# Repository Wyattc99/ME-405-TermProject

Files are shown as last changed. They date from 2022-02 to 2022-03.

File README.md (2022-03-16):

# Term Project
## Authors: Wyatt Conner, Jameson Spitz, Jacob Wong

## Introduction
The purpose of this project was to design a 2D plotter that can interpret an HPGL file and 
draw an image on paper. Our system controls the position of a pen by having our Nucleo 
microcontroller drive two motors, moving the pen along 2 axes. Additionally, the system 
must raise and lower the pen to control when the system is drawing.

## Hardware Design
To control the position of a pen, we designed a two degree of freedom system that operates 
in cylindrical coordinates R and Theta. We drive a lead screw actuator system using a motor 
to move the pen along the radial direction. The pen is secured to a 3D printed housing that 
is pushed by the lead screw along the main shaft of the assembly. The housing also holds a 
solenoid that performs the pen-up/pen-down action of the system.

To control movement of the housing in the theta direction, our system revolves about a pin joint 
connected to one end of a shaft, and a second motor drives a wheel on the other end of the shaft. 
See the images below for a CAD model and an image of the final prototype. All parts were either 
bought online, 3D printed, or found in our local Cal Poly machine shops.

### Assembly CAD Drawing
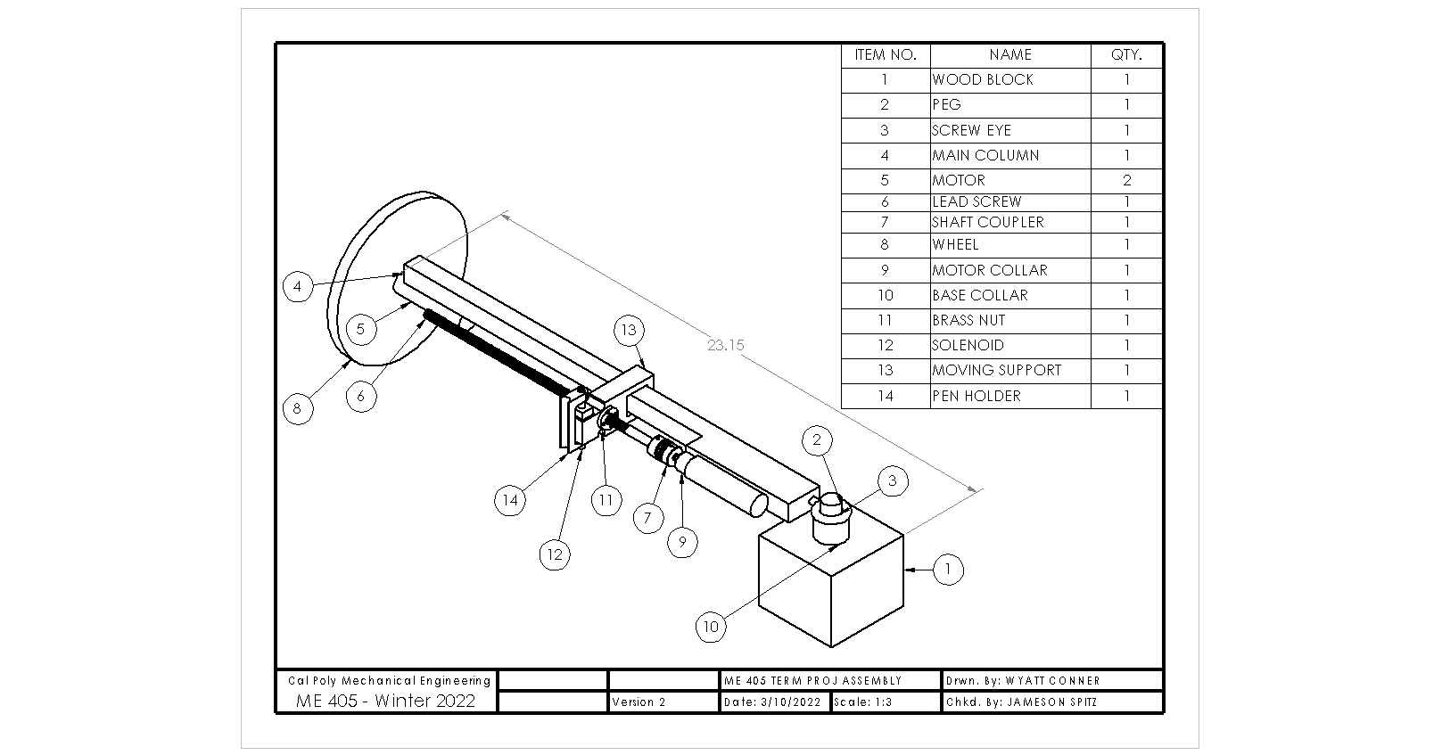
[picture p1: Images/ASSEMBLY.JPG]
Assembly Drawing and BOM


### Physical System Designed
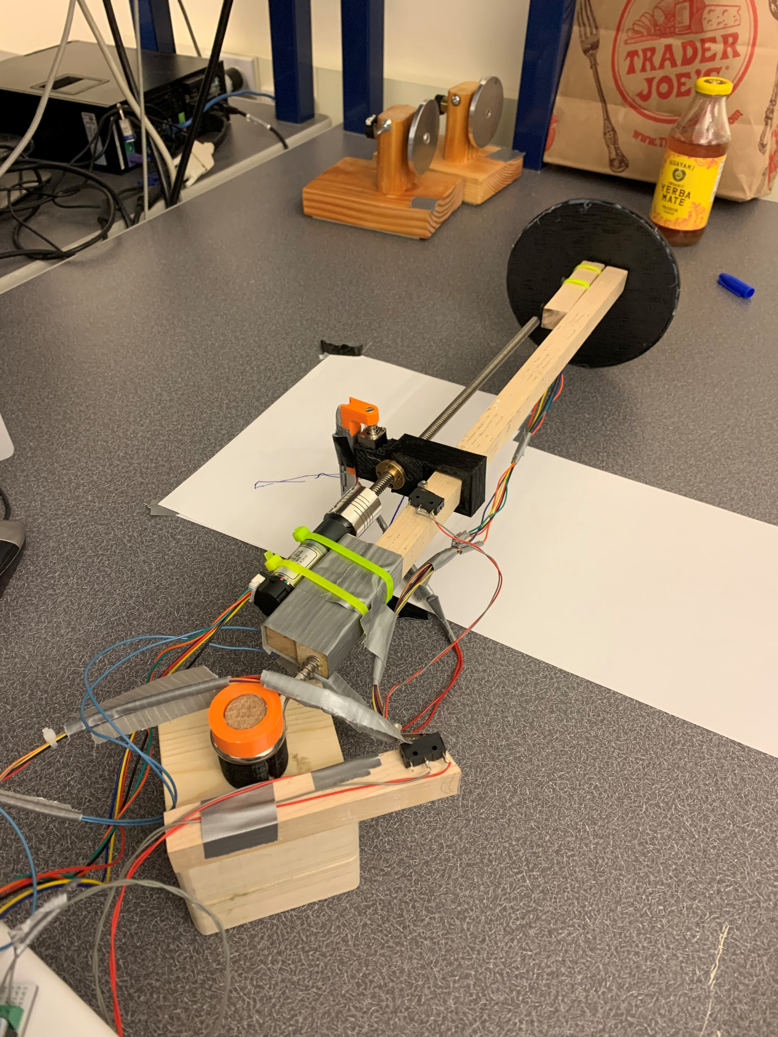
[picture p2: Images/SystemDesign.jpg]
System Design


We needed 12V to power the solenoid. However,  the Nucleo is unable to provide such a voltage. 
Therefore, we use an external 12V-DC power supply, and we constructed circuitry using a MOSFET to 
control this voltage to the solenoid. This allows us to power and unpower the solenoid by setting 
a pin to high or low on the microcontroller. The schematic of the circuitry is shown below.

### Solenoid Wiring Diagram (Transistor and Diode)
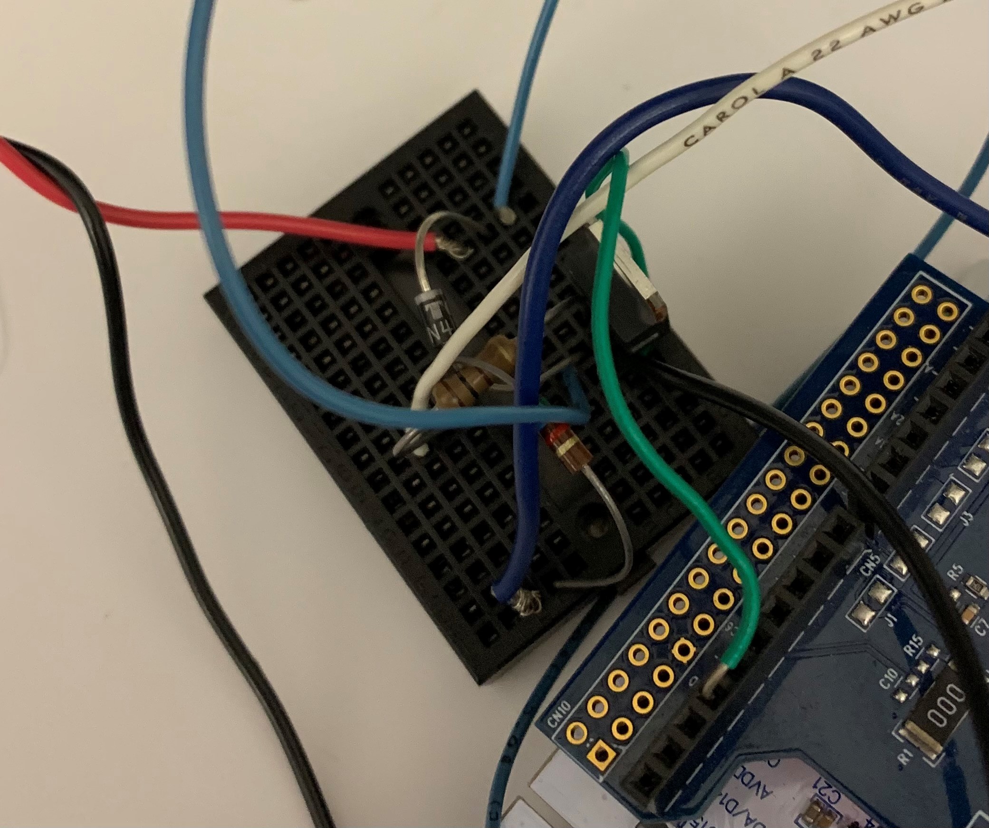
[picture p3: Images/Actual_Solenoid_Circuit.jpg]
Solenoid Wiring1


### Theoretical Wiring Diagram
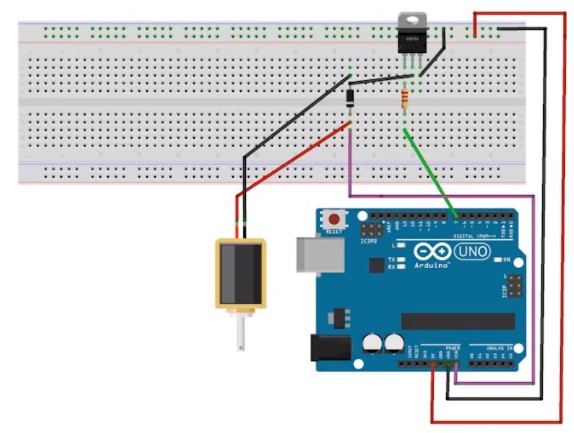
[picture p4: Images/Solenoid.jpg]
Solenoid Wiring2


Lastly, a limit switch is mounted on the main shaft to establish the zero point of the radial 
direction. Whenever the pen housing unit hits the limit switch, it sends a signal to the 
microcontroller to let the software know that housing is at this point.

## Software Design
The software for this project is a cooperative multitasking system that contains five tasks: a 
zeroing task, two tasks to set the desired position of the motors, and two tasks to set the duty
cycle of the motors. The zeroing task named 'Zero Position' sets the encoder position to zero
when the pen housing hits a limit switch, marking the zero position in the radial direction. The
desired position tasks called 'Radial Set Point Control' and 'Theta Set Point Control' reads the
HPGL file and converts X and Y coordinates to R and Theta coordinates. Then, the tasks store 
these coordinates in two queue objects. The two duty cycle tasks, called 'Radial Position Control'
and 'Theta Position Control' gather encoder data and desired position data from the previous two 
tasks. These tasks then implement closed-loop positional control to set the duty cycle going to 
each motor.

To convert X and Y data from the HPGL to R and Theta coordinates in the 'Set Point Control' 
tasks, we needed to derive two kinematic equations, one for R and one for Theta. Hand calculations
for these equations are pictured below.

### Inverse Kinematics Calculations
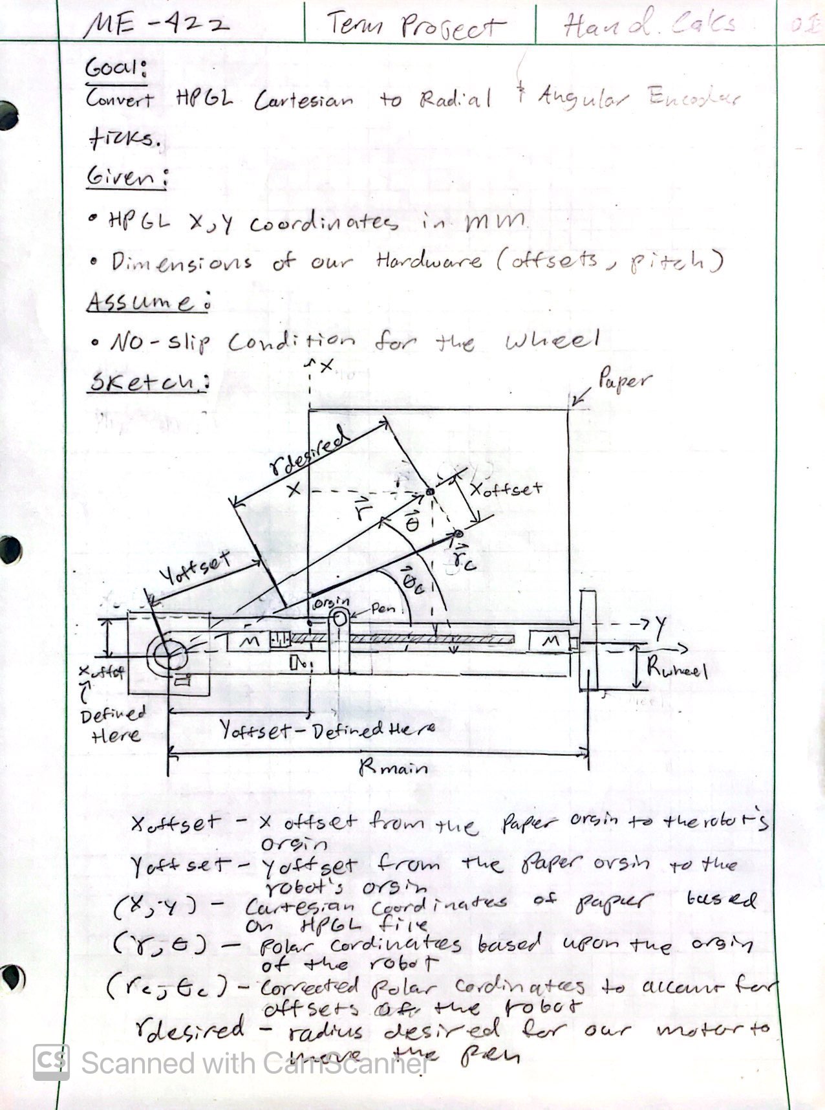
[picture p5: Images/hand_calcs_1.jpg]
Kinematics Sheet 1

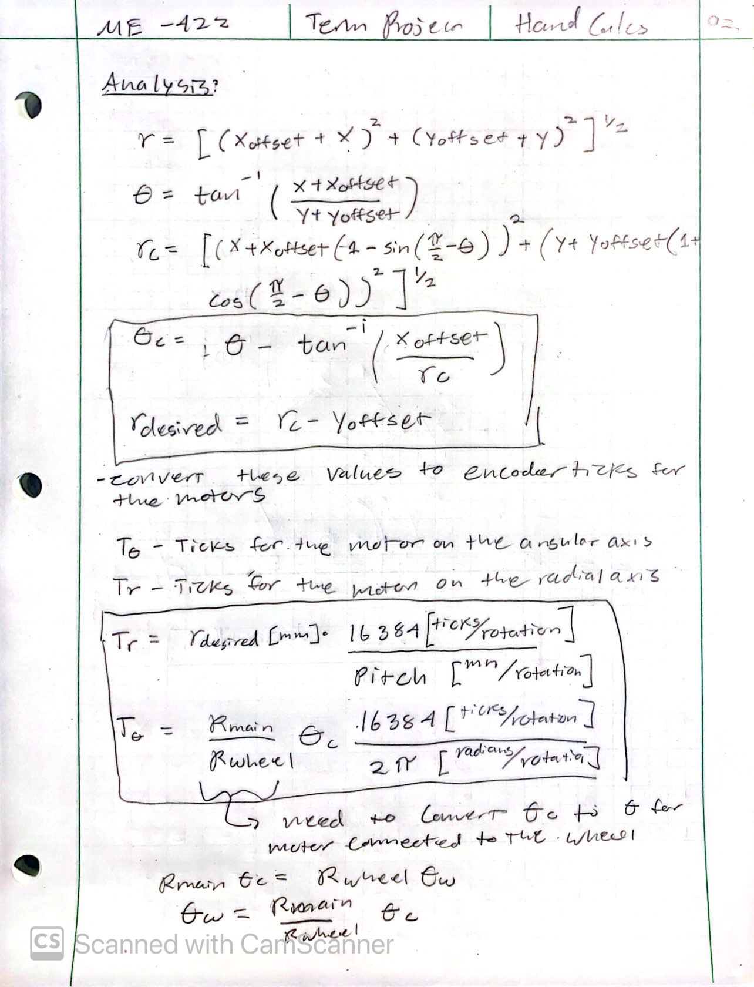
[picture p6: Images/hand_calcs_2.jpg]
Kinematics Sheet 2


Each task is run using a finite state machine (FSM). The most important FSMs are in the 'Radial 
Position Control' and 'Theta Position Control' tasks. Both these task run using a similar FSM 
depicted by the State Transition Diagrm in the image below. In State 0, each task collects a new 
set point, or desired position for the motor. In State 1, each task calculates the error between
actual position (encoder data) and set point. If the error is above a specified threshold, it 
updates the duty cycle of the motor based on the error and returns to State 1. If the error is 
below the threshold, the tasks returns to State 0 to get a new set point. 

See a full description of our software and FSM and Task Diagram in the link to our repository:[Github Pages](https://wyattc99.github.io/ME-405-TermProject/)

## Results
To test our system, we began with testing each individual component separately. We first ran each 
motor to verify that we can control them separately. We next isolated the solenoid to ensure we 
can power and unpower it using the microcontroller. Lastly, we tested the limit switch by itself
and checked if the software can properly detect collision. 

Once we were ready to test the entire system together, our main focus was to verify that our 
kinematic relationships gave accurate results, adjust our threshold value for the error, and to 
tune the controller gains from our positional control loop. This test proved to be challenging,
and unfortunately, our system was unable to achieve satisfactory results. The desired image we
drew in Inkscape was a rectangle, but the image below is the drawing that our system produced.

### Resulting Rectangle
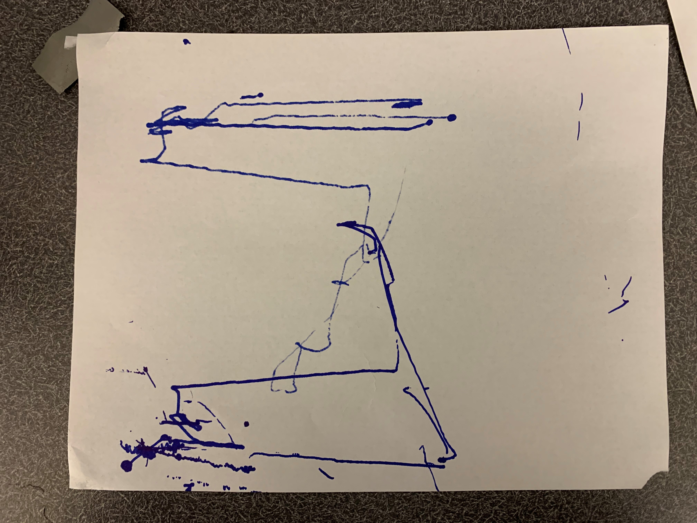
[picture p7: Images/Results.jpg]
Results


## Conclusion and Discussion
Although we were unable to create a successful 2D plotter before the deadline, we found several
issues that could be rectified in the future. One problem that we noticed was that the two
motors would reach their set points out of sync, meaning that one motor would have to wait for 
the other motor. To solve this, we could have interpolated between two setpoints to create 
several 'inbetween setpoints'. This would reduce the inaccuracies caused by the motors meeting
their setpoints at different times.

Another way we could have improved our software was to change the type of controller we used
in our positional control loop. Our current software uses a proportional (P) controller. Instead,
we could have implemented a PI controller to reduce the steady-state positional error. We could 
have even implemented a PID controller to decreased overshoot.

## Bill Of Materials

| Qty. | Part | Source | Est. Cost |
|:----:|:---  |:---|:---:|
|  1 | Wheel | 3D Printing | - |
|  1 | Screw Eye | Home Depot | $4.99 |
|  1 | Lead Screw | Amazon | $12.99  |
|  1 | Solenoid | Digi-Key | $4.95 |
|  3 | Limit Switches | Amazon | $2.00 |
|  1 | Shaft Slider | 3D Printing | - |
|  1 | Pencil/Solenoid Housing | 3D Printing | - |
|  1 | Duct Tape | Home Depot | $6.87 |
|  2 | MOSFET | Friend in 405 | - |
|  1 | Diode | ME 405 Lab | - |
|  3 | Zip Ties | Friend in 405 | - |
|  5 | Wires/Solder | ME 405 Lab | - |
|  2 | Motors | ME 405 Lab | - |
|  1 | Wood Block | Home Depot | $8.25 |
|  1 | Shaft | Home Depot | $6.18 |
|  1 | Shaft Coupler | Amazon | $3.98 |
|  1 | Wooden Peg | Home Depot | $3.48 |

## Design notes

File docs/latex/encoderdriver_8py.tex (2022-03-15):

\hypertarget{encoderdriver_8py}{}\doxysection{src/encoderdriver.py File Reference}
\label{encoderdriver_8py}\index{src/encoderdriver.py@{src/encoderdriver.py}}

This file configures Nucleo pins, timers, and channels for so that it can send voltage to a motor.  

\doxysubsection*{Classes}
\begin{DoxyCompactItemize}
\item 
class \mbox{\hyperlink{classencoderdriver_1_1_encoder_driver}{encoderdriver.\+Encoder\+Driver}}
\begin{DoxyCompactList}\small\item\em Initializes encoder pins, timer, and channel. \end{DoxyCompactList}\end{DoxyCompactItemize}
\doxysubsection*{Variables}
\begin{DoxyCompactItemize}
\item 
\mbox{\Hypertarget{encoderdriver_8py_af3a4bb5350815afb8f1333f182316c40}\label{encoderdriver_8py_af3a4bb5350815afb8f1333f182316c40}} 
{\bfseries encoderdriver.\+my\+\_\+encoder1} = Encoder\+Driver(pyb.\+Pin.\+board.\+PB6, pyb.\+Pin.\+board.\+PB7, 4)
\begin{DoxyCompactList}\small\item\em my\+\_\+encoder1 Encoder object 1. \end{DoxyCompactList}\item 
\mbox{\Hypertarget{encoderdriver_8py_abfefff0f805f0b7f8a9dd10919517436}\label{encoderdriver_8py_abfefff0f805f0b7f8a9dd10919517436}} 
{\bfseries encoderdriver.\+my\+\_\+encoder2} = Encoder\+Driver(pyb.\+Pin.\+board.\+PC6, pyb.\+Pin.\+board.\+PC7, 8)
\begin{DoxyCompactList}\small\item\em my\+\_\+encoder2 Encoder object 2. \end{DoxyCompactList}\end{DoxyCompactItemize}

\doxysubsection{Detailed Description}
This file configures Nucleo pins, timers, and channels for so that it can send voltage to a motor. 

Can send a PWM duty cycle to the motor to control how fast the motor spins. Uses a L6206 motor shield to control motor direction. \begin{DoxyAuthor}{Author}
Jacob Wong 

Wyatt Conner 

Jameson Spitz 
\end{DoxyAuthor}
\begin{DoxyDate}{Date}
26-\/Jan-\/22 
\end{DoxyDate}
\begin{DoxyCopyright}{Copyright}
by Jacob Wong all rights reserved 
\end{DoxyCopyright}

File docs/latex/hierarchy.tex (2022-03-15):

\doxysection{Class Hierarchy}
This inheritance list is sorted roughly, but not completely, alphabetically\+:\begin{DoxyCompactList}
\item \contentsline{section}{task\+\_\+share.\+Base\+Share}{\pageref{classtask__share_1_1_base_share}}{}
\begin{DoxyCompactList}
\item \contentsline{section}{task\+\_\+share.\+Queue}{\pageref{classtask__share_1_1_queue}}{}
\item \contentsline{section}{task\+\_\+share.\+Share}{\pageref{classtask__share_1_1_share}}{}
\end{DoxyCompactList}
\item \contentsline{section}{encoderdriver.\+Encoder\+Driver}{\pageref{classencoderdriver_1_1_encoder_driver}}{}
\item \contentsline{section}{read\+\_\+plotter.\+Hpgl}{\pageref{classread__plotter_1_1_hpgl}}{}
\item \contentsline{section}{limit\+\_\+switch.\+Limit\+\_\+\+Switch}{\pageref{classlimit__switch_1_1_limit___switch}}{}
\item \contentsline{section}{motordriver.\+Motor\+Driver}{\pageref{classmotordriver_1_1_motor_driver}}{}
\item \contentsline{section}{positioncontrol.\+Position\+Control\+Task}{\pageref{classpositioncontrol_1_1_position_control_task}}{}
\item \contentsline{section}{solenoid.\+Solenoid}{\pageref{classsolenoid_1_1_solenoid}}{}
\item \contentsline{section}{cotask.\+Task}{\pageref{classcotask_1_1_task}}{}
\item \contentsline{section}{cotask.\+Task\+List}{\pageref{classcotask_1_1_task_list}}{}
\end{DoxyCompactList}

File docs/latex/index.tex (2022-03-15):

\hypertarget{index_sec_intro1}{}\doxysection{Software Design}\label{index_sec_intro1}
\begin{DoxyVerb}                        Our program will consist of tasks position_control1, position_control2, encoder1, encoder2, and HP-GL. 
                        The position control tasks will control the duty cycle of each motor individually and measure 
                        how many ticks each encoder is from its desired position. As each encoder gets closer to its 
                        desired position, the duty cycles will be decreasing to reach a final position without overshoot 
                        through closed loop position control. The encoder tasks will be responsible for updating, reading, 
                        and setting encoder position for each motor. A critical part to this project is finding a way to 
                        reset the set position for each motor based on the image we want to draw. We imagine that we will 
                        be using a task that gets the desired pencil position through HP-GL, which tells us the set position 
                        in the radial and theta direction for each move of the pencil. Additionally, we will have a solenoid 
                        driver to control whether the solenoid is on or off to move the pencil on and off the paper. Finally, 
                        a limit switch driver will read when the pencil has reached the end of the leadscrew, notifying the 
                        controller the motor needs to stop or switch direction to avoid system failure. 

                        All tasks will be facilitated by a main program that runs each task through a task scheduler. 
                        Additionally, all shared and queued variables will be created within the main file. We expect each 
                        task to share encoder position and duty cycle to control the motor speed. Additionally, there will 
                        be queue values to store encoder position and time data that will be printed at the end of a program run. 

                        With all tasks running simultaneously at different frequencies through the task scheduler, our microcontroller 
                        should be able to successfully control each motor's speed and direction individually to move our pencil in 
                        the radial and theta direction. The most difficult aspect of the code we envision is changing the desired position 
                        of each encoder based on the image we want the system to draw. We will need gain factors to convert a desired 
                        pencil position into radial and axial coordinates and then convert into encoder ticks. These gain values will be 
                        found through testing.
\end{DoxyVerb}
\hypertarget{index_subsec_intro2}{}\doxysection{Task Diagram and Finite State Machines}\label{index_subsec_intro2}
\begin{DoxyVerb}                        Below is the Task Diagram of all tasks used to control the pencil position.
                        \image html TaskDiagram_FinalProj.png

                        Below is the Finite State Machine for our the position control file of one motor.
                        \image html Fsm_TermProj.png
\end{DoxyVerb}
 \begin{DoxyAuthor}{Author}
Jameson Spitz 

Jacob Wong 

Wyatt Conner
\end{DoxyAuthor}
\begin{DoxyCopyright}{Copyright}
CC BY
\end{DoxyCopyright}
\begin{DoxyDate}{Date}
February 24, 2021 
\end{DoxyDate}

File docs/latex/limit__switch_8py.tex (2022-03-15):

\hypertarget{limit__switch_8py}{}\doxysection{src/limit\+\_\+switch.py File Reference}
\label{limit__switch_8py}\index{src/limit\_switch.py@{src/limit\_switch.py}}

This file configures a limit switch to trigger high when our physical system presses the limit switch closed.  

\doxysubsection*{Classes}
\begin{DoxyCompactItemize}
\item 
class \mbox{\hyperlink{classlimit__switch_1_1_limit___switch}{limit\+\_\+switch.\+Limit\+\_\+\+Switch}}
\begin{DoxyCompactList}\small\item\em Initializes the normally open pin on the Nucleo as an input pin. \end{DoxyCompactList}\end{DoxyCompactItemize}
\doxysubsection*{Variables}
\begin{DoxyCompactItemize}
\item 
\mbox{\Hypertarget{limit__switch_8py_a87c9bd543d8a042600c67cf8071ea98a}\label{limit__switch_8py_a87c9bd543d8a042600c67cf8071ea98a}} 
{\bfseries limit\+\_\+switch.\+my\+\_\+lim\+\_\+A} = Limit\+\_\+\+Switch(pyb.\+Pin.\+board.\+PC0)
\item 
\mbox{\Hypertarget{limit__switch_8py_aa92905b475b2bf1bbdf7b00949fcc1cc}\label{limit__switch_8py_aa92905b475b2bf1bbdf7b00949fcc1cc}} 
{\bfseries limit\+\_\+switch.\+my\+\_\+lim\+\_\+B} = Limit\+\_\+\+Switch(pyb.\+Pin.\+board.\+PB0)
\end{DoxyCompactItemize}

\doxysubsection{Detailed Description}
This file configures a limit switch to trigger high when our physical system presses the limit switch closed. 

The file is set up as a class so a user can instantiate mulitple limit switches. We have physically configured the limit switch to be normallly open. \begin{DoxyAuthor}{Author}
Jacob Wong 

Wyatt Conner 

Jameson Spitz 
\end{DoxyAuthor}
\begin{DoxyDate}{Date}
5-\/March-\/22 
\end{DoxyDate}
\begin{DoxyCopyright}{Copyright}
by Jacob Wong all rights reserved 
\end{DoxyCopyright}

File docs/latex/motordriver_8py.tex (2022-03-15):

\hypertarget{motordriver_8py}{}\doxysection{src/motordriver.py File Reference}
\label{motordriver_8py}\index{src/motordriver.py@{src/motordriver.py}}

This file configures Nucleo pins, timers, and channels for so that it can send voltage to a motor.  

\doxysubsection*{Classes}
\begin{DoxyCompactItemize}
\item 
class \mbox{\hyperlink{classmotordriver_1_1_motor_driver}{motordriver.\+Motor\+Driver}}
\begin{DoxyCompactList}\small\item\em Initializes motor pins allowing for the motor to rotate in both directions. \end{DoxyCompactList}\end{DoxyCompactItemize}
\doxysubsection*{Variables}
\begin{DoxyCompactItemize}
\item 
\mbox{\Hypertarget{motordriver_8py_ad9e5193122e62bbfef90dec601759637}\label{motordriver_8py_ad9e5193122e62bbfef90dec601759637}} 
{\bfseries motordriver.\+motor1} = Motor\+Driver(pyb.\+Pin.\+board.\+PB5, pyb.\+Pin.\+board.\+PB4, pyb.\+Pin.\+board.\+PA10, 3)
\begin{DoxyCompactList}\small\item\em motor1 Motor object 1. \end{DoxyCompactList}\item 
\mbox{\Hypertarget{motordriver_8py_a6af998346fc8903e2ad3fde4cac66cfd}\label{motordriver_8py_a6af998346fc8903e2ad3fde4cac66cfd}} 
{\bfseries motordriver.\+motor2} = Motor\+Driver(pyb.\+Pin.\+board.\+PA0, pyb.\+Pin.\+board.\+PA1, pyb.\+Pin.\+board.\+PC1, 5)
\begin{DoxyCompactList}\small\item\em motor2 Motor object 2. \end{DoxyCompactList}\end{DoxyCompactItemize}

\doxysubsection{Detailed Description}
This file configures Nucleo pins, timers, and channels for so that it can send voltage to a motor. 

Can send a PWM duty cycle to the motor to control how fast the motor spins. Uses a L6206 motor shield to control motor direction. \begin{DoxyAuthor}{Author}
Jacob Wong 

Wyatt Conner 

Jameson Spitz 
\end{DoxyAuthor}
\begin{DoxyDate}{Date}
26-\/Jan-\/22 
\end{DoxyDate}
\begin{DoxyCopyright}{Copyright}
by Jameson Spitz all rights reserved 
\end{DoxyCopyright}

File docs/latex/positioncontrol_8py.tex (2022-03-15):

\hypertarget{positioncontrol_8py}{}\doxysection{src/positioncontrol.py File Reference}
\label{positioncontrol_8py}\index{src/positioncontrol.py@{src/positioncontrol.py}}

Control Motor\textquotesingle{}s position based on desired HPGL set points.  

\doxysubsection*{Classes}
\begin{DoxyCompactItemize}
\item 
class \mbox{\hyperlink{classpositioncontrol_1_1_position_control_task}{positioncontrol.\+Position\+Control\+Task}}
\begin{DoxyCompactList}\small\item\em This class contains the methods to create a feed back control system using a motor and encoder. \end{DoxyCompactList}\end{DoxyCompactItemize}

\doxysubsection{Detailed Description}
Control Motor\textquotesingle{}s position based on desired HPGL set points. 

The file can check if the error between a motor position and the setpoint is within reasonable limits and flag for the next setpoint. We use a simple proportional controller to set a proper duty cycle based on the magnitude of the error. \begin{DoxyAuthor}{Author}
Jacob Wong 

Wyatt Conner 

Jameson Spitz 
\end{DoxyAuthor}
\begin{DoxyDate}{Date}
3-\/Mar-\/22 
\end{DoxyDate}
\begin{DoxyCopyright}{Copyright}
by Jameson Spitz all rights reserved 
\end{DoxyCopyright}

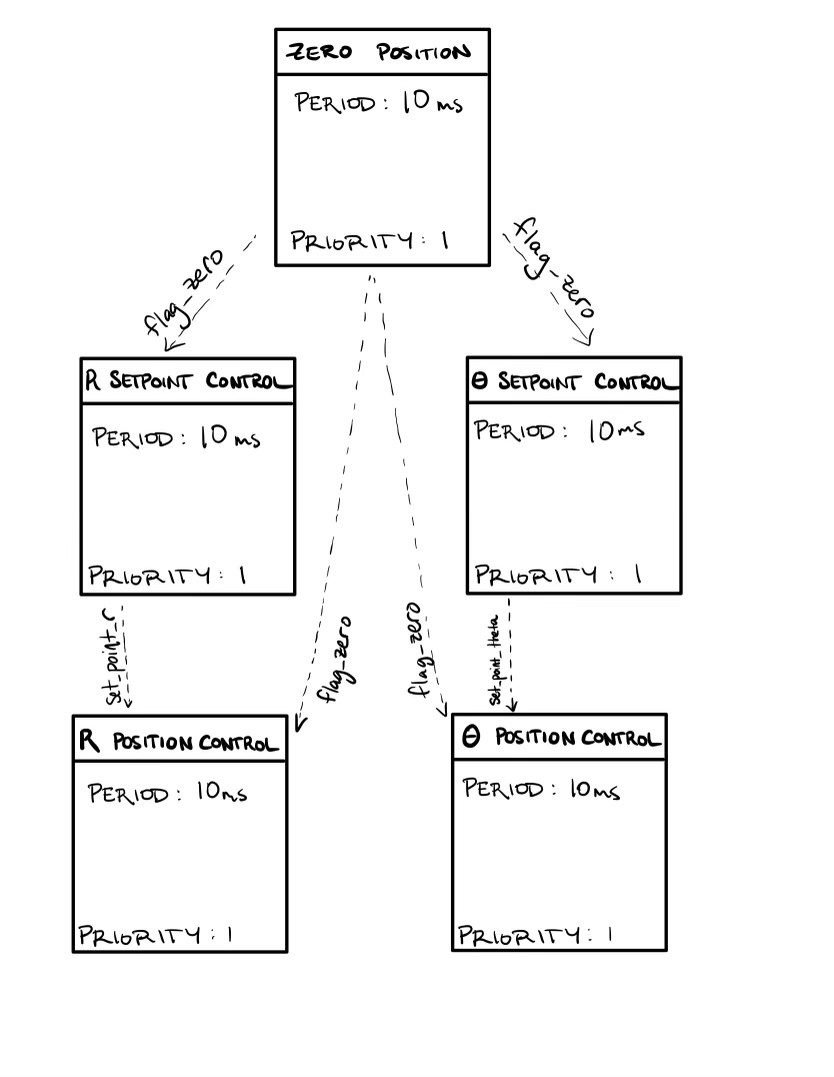
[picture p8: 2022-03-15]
docs/TaskDiagram_FinalProj.jpg

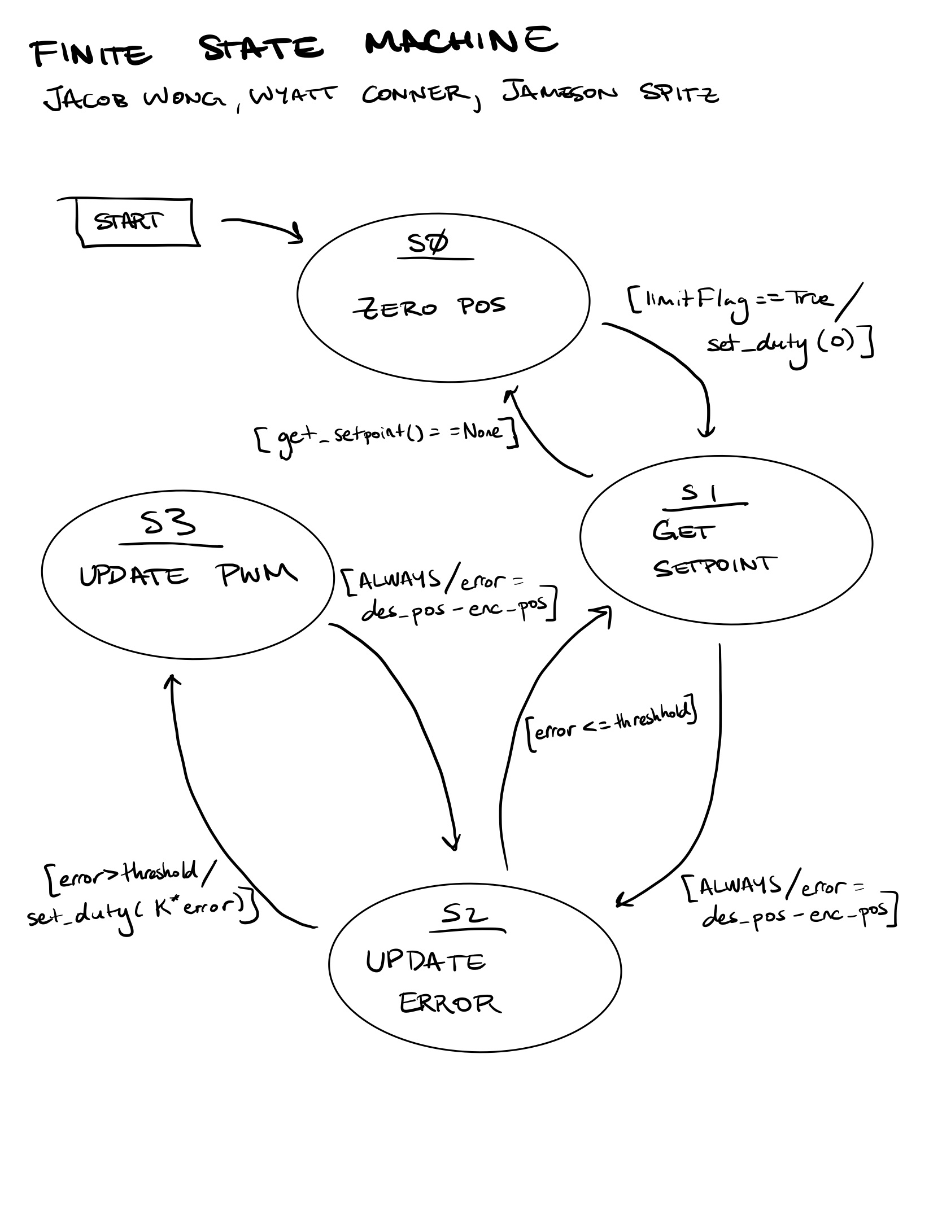
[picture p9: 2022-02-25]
Images/Fsm_TermProj.png

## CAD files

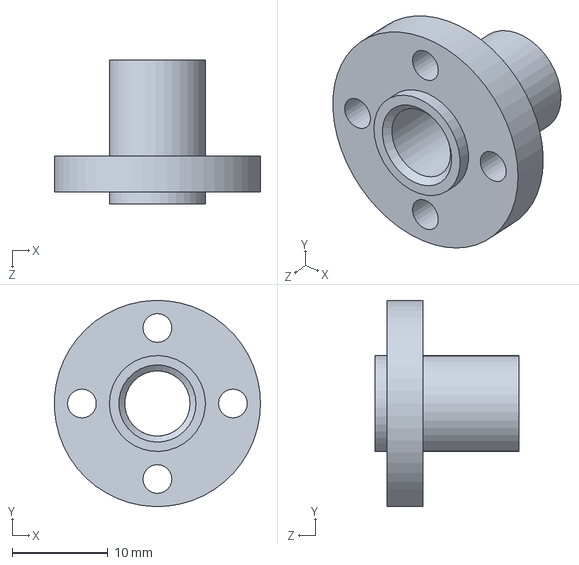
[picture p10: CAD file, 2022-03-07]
CAD/Version 2/BrassNut.SLDPRT
21.5 x 21.5 x 15.0 mm

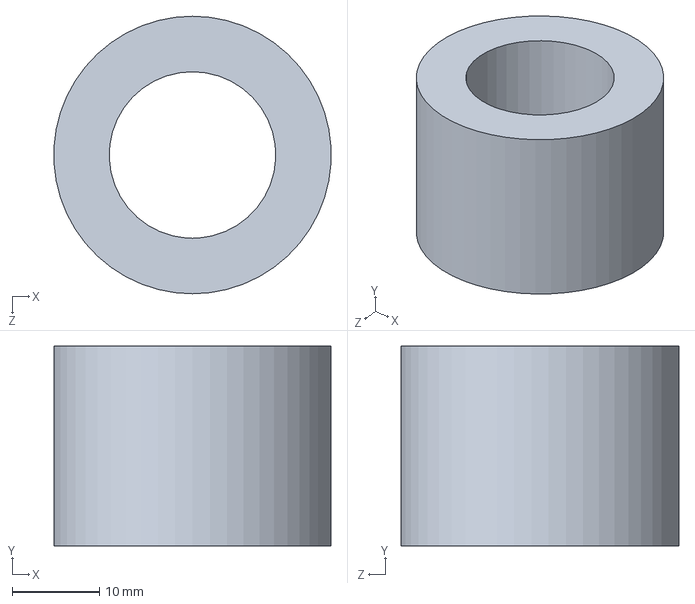
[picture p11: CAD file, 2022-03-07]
CAD/Version 2/Collar2.SLDPRT
31.7 x 22.9 x 31.8 mm

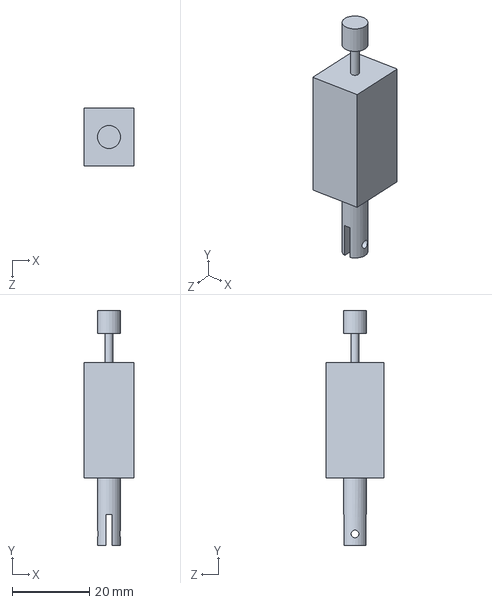
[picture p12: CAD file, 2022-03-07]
CAD/Version 2/Solenoid.SLDPRT
13.0 x 61.0 x 15.0 mm

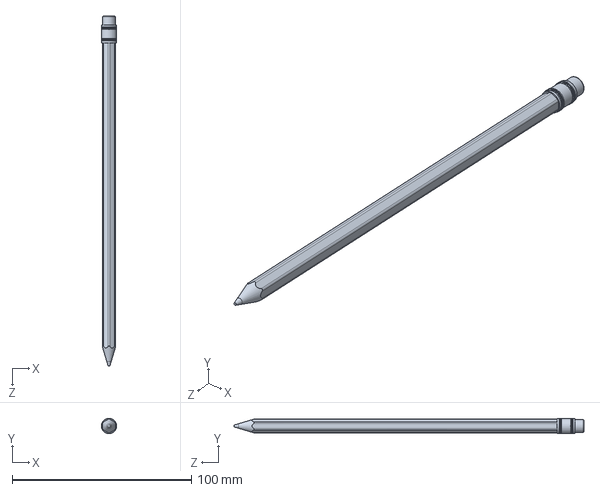
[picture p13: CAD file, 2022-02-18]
CAD/Version 2/Pencil.SLDPRT
8.60 x 8.59 x 195.0 mm

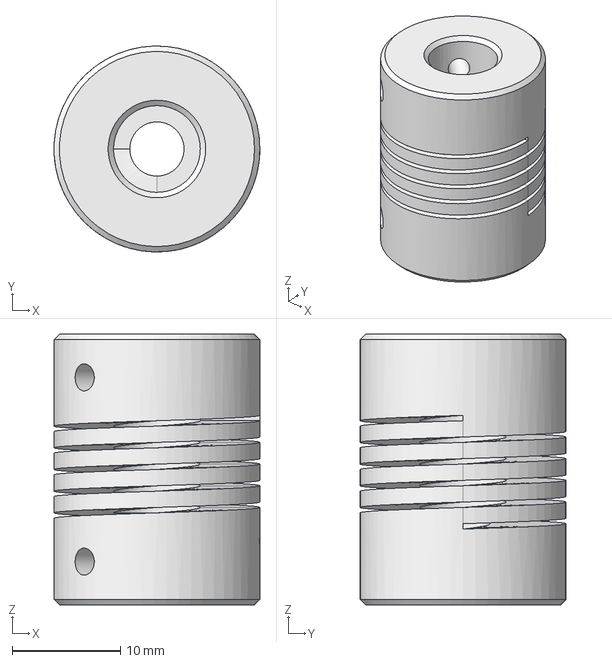
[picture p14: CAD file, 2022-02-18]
CAD/Version 2/flex-coupler-5-8mm.step
19.0 x 19.0 x 25.0 mm

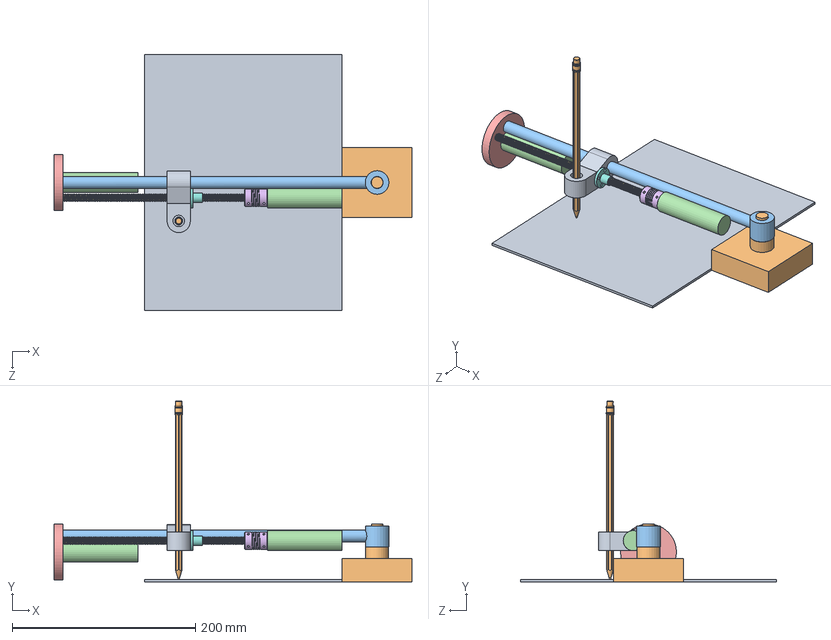
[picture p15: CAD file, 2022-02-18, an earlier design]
CAD/Version 1/ME 405 Term Project.SLDASM
391.0 x 197.5 x 279.4 mm
Wood Block
Clevis Joint
Motor x 2
Wheel
flex-coupler-5-8mm.step
LeadScrew2 8mm x 2mmPitch 500
Nut.ipt
Nut_Rod Connector
Pencil

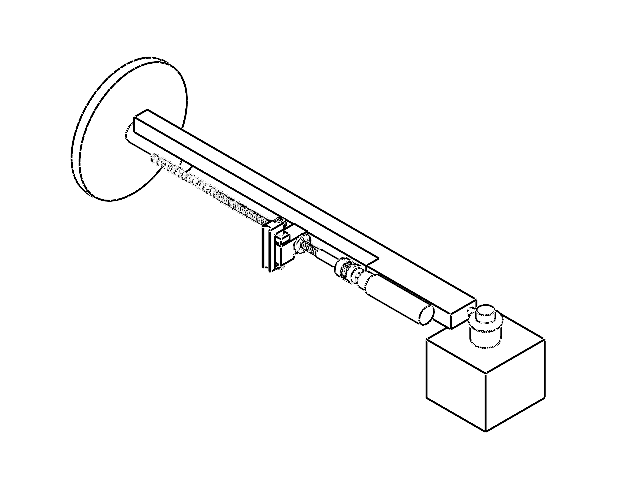
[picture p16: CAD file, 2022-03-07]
CAD/Version 2/Assembly_V2.SLDASM
Base_Plate
PEG
Collar
Main Shaft
Motor x 2
LeadScrew2 8mm x 2mmPitch 500
flex-coupler-5-8mm.step
Wheel
Motor to Collar Fit
Collar2
BrassNut
Solenoid
Omega part^Assembly_V2
pen holder^Assembly_V2

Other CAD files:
CAD/Version 2/Main Shaft.SLDPRT
CAD/Version 2/1001.SLDPRT
CAD/Version 2/Copy of Copy of Motor Coupler.SLDPRT
CAD/Version 2/Wheel.SLDPRT
CAD/Version 2/Motor to Collar Fit.SLDPRT
CAD/Version 2/PEG.SLDPRT
CAD/Version 2/Collar.SLDPRT
CAD/Version 2/Base_Plate.SLDPRT
CAD/Version 2/Motor.SLDPRT
CAD/Version 2/Nut_Rod Connector.SLDPRT
CAD/Version 1/Clevis Joint.SLDPRT
CAD/Version 1/LeadScrew2 8mm x 2mmPitch 500.SLDPRT
CAD/Version 1/ME 405 Term Project.SLDDRW
CAD/Version 1/Motor.SLDPRT
CAD/Version 1/Nut.ipt
CAD/Version 1/Nut_Rod Connector.SLDPRT
CAD/Version 1/Wheel.SLDPRT
CAD/Version 1/Wood Block.SLDPRT

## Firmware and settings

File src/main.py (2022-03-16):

"""!
@file main.py
The main file of the term project that creates and runs the tasks needed to control
the 2 axis drawing robot we created. To do this we create each task as a method
that interacts with the firmware, and these tasks are then ran using cotask. 
@author Wyatt Conner
@author Jacob Wong
@author Jameson Spitz
@date 5-Mar-22
@copyright by Jameson Spitz all rights reserved

"""

import cotask
import task_share
from positioncontrol import PositionControlTask
from encoderdriver import EncoderDriver
from motordriver import MotorDriver
from limit_switch import Limit_Switch
from solenoid import Solenoid
import pyb
import gc
import read_plotter
import time

def zero_position():
    """!
    When this task is called it will zero the 2 axis drawing robot back to its
    orgin which is located by 2 limit switches along its radial axis and angular
    axis. Once each limit switch has been touched the method will terminate and
    turn off each motor. 
    """
    
    ## Zero B is a flab to show that the motor B has finished its zeroing process
    zero_B = False
    print('Beginning Zeroing Proccess')
    
    ## State of the Zero Position Method to determine what state the finite state machine is in
    state = 0
    
    while True:
        
        # if (limit_A.check_limit()):
        # 210, 297 mm
        # set the duty to be constant until it hits the switch for motor A
        
        # Check the limit switch if it has been triggered
        if (state == 0):
        # set the duty to be constant until it hits the switch for motor B
            print(limit_flag_B.get())
            limit_flag_B.put(limit_B.check_limit())
            
            # Turn the motor on if the flag is off and has never been turned on
            if limit_flag_B.get() == 0 and zero_B == False:
                pass
                motor_B.set_duty_cycle(45)
            
            # Turn the motor off and set the encoder positions
            elif limit_flag_B.get() == 1:
                motor_B.set_duty_cycle(0)
                ## Zero_B is a flag to represent once the limit switch has been turned on once this flag will remain on to prevent oscillations of the switch
                zero_B = True
                enc_B.set_position(-3000)
                
                state = 1
                
                
        # Print the encoder positions to ensure they are zero'd
        if (state == 1):
            print(enc_A.get_position())
            print(enc_B.get_position())
            flag_zero.put(1)
            state=2
            
        if (state==2):
            pass
        
        print('1')
        yield(0)
    # Set the encoder position Values to Zero
    
def update_pwm_radial ():
    """!
    Task which facilitates the motor position control method and records
    motor 1 data in a queue. The task then prints the data which is controlled
    by a generator.
    """
    
    ## State varible used to signal program whether to collect data, print or when to terminate the method
    state = 5
    
    while True:
        
        # We will remain in state 5 until the machine is zero'd to begin drawing.
        if (state == 5):
            if (flag_zero.get() == 1):
                state = 0
        # State 0 is when we begin to control each motor for our set data points. 
        elif(state == 0):
            
            # Runs position control function from positioncontrol.py
            control_radial.position_control()
            
            if(radial_hpgl.empty()):
                state = 1
                
            if(flag_radial.get() == 0):
                state = 2
    
        elif(state == 1):
            motor_B.set_duty_cycle(0)
            
        elif(state == 2):
            motor_B.set_duty_cycle(0)
            
            if(flag_radial.get() == 1):
                state = 0
                
        elif(state == 3):
            print('Limit Has been hit!')
            state = 0

        #print('State: ', state)
        print('2')
        yield (0)
        
def update_pwm_theta ():
    """!
    This is the method that controls the motor along the angular axis of the robot.
    This is done by updating the set point for the motor once each motor as reached
    their previous set points. Then conduct position control on the motor until it hits
    its new set point, then turn off the motor and wait for the radial axis to hit its set
    point. 
    """
    
    ## State varible used to signal program whether to collect data, print, data, or terminate program.
    state = 5
    
    while True:
        
        if (state == 5):
            if (flag_zero.get() == 1):
                state = 0
                
        
        elif(state == 0):
            
            # Runs position control function from positioncontrol.py
            control_theta.position_control()
            
            if(theta_hpgl.empty()):
                    state = 1
                    
            if(flag_theta.get() == 0):
                state = 2
        
        elif(state == 1):
            motor_A.set_duty_cycle(0)
            
        elif(state == 2):
            motor_A.set_duty_cycle(0)
            
            if(flag_theta.get() == 1):
                state = 0
            
        elif(state == 3):
            state = 0
        print('3')
        yield (0)
        
def get_setpoint_r ():
    """!
    This method is used to control the motor along the radial axis of the robot.
    The way this is done is that the set point is given from our read plotter file.
    We then conduct a position control for this set point and once the motor is
    within a window of error that is acceptable the motor will turn off and set
    a flag that it has meet it's set point. Once both motors have meet their set
    points they will then update to a new setpoint and do the entire process again. 
    """
    ## State varible used to signal program whether to collect data, print, data, or terminate program.
    state = 5
        
    while True:
        
        
        if (state == 5):
            if (flag_zero.get() == 1):
                state = 0
                
        elif(state == 0):
            
            set_point_r.put(radial_hpgl.get())
            set_point_theta.put(theta_hpgl.get())
            # print('Radial Set Point: ', set_point_r.get())
            state = 1
            
        elif(state == 1):
        
            ## Condition 1 checks if the radial motor is within its acceptable error limit to say it has meet its set point.
            condition1 = control_radial.check_error()
            
            if(condition1 == True):
                state = 2
                
        elif(state == 2):
            flag_radial.put(0)
            ## Condition 2 checks if the theta motor is within its acceptable error limit to say it has meet its set point. 
            condition2 = control_theta.check_error()
            print('Motor Radial')
            
            if (condition2 == True):
                state = 0
                flag_radial.put(1)
                print('!!!!!!!!!!!!!!!!! Checkpoint !!!!!!!!!!!!!!!!!')
                sol_pos = solenoid_hpgl.get()
                print('Sol: ', sol_pos)
                if sol_pos == 0:
                    my_sol.pen_up()
                elif sol_pos==1:
                    my_sol.pen_down()
    
        print('4')        
        yield(0)
                
def get_setpoint_theta ():
    """!
    This method is used to update the set point of the motor on the theta axis.
    If both motors have reached their setpoints this method will update the
    setpoint of the theta motor. The set point data is provided from the read 
    plotter file. 
    """
    
    ## State varible used to signal program whether to collect data, print, data, or terminate program.
    state = 5
        
    while True:
        
        if (state == 5):
            if (flag_zero.get() == 1):
                state = 0
                
        elif(state == 0):
            set_point_theta.put(theta_hpgl.get())
            state = 1
            
        elif(state == 1):
            ## Condition 2 checks if the theta motor is within its acceptable error limit to say it has meet its set point. 
            condition2 = control_theta.check_error()
            
            if (condition2 == True):
                state = 2
                
        elif(state == 2):
            flag_theta.put(0)
            ## Condition 1 checks if the radial motor is within its acceptable error limit to say it has meet its set point.
            condition1 = control_radial.check_error()
            print('Motor Theta')
             
            if (condition1 == True):
                state = 0
                flag_theta.put(1)
                print('!!!!!!!!!!!!!!!!! Checkpoint !!!!!!!!!!!!!!!!!')
        print('5')
        #print(state)        
        yield(0)
    

if __name__ == "__main__":
    print ('\033[2JTesting ME405 stuff in cotask.py and task_share.py\r\n'
           'Press ENTER to stop and show diagnostics.')
    
    ## This a Queue of encoder tick set points for the radial motor converted from hpgl file.
    radial_hpgl = task_share.Queue('f', size = 250, thread_protect = False,
                                      overwrite = False, name = 1)
    
    ## This a Queue of encoder tick set points for the angular motor converted from hpgl file.
    theta_hpgl = task_share.Queue('f', size = 250, thread_protect = False,
                                      overwrite = False, name = 2)
    
    ## This creates a queue for the solenoid to instruct when the solenoid should be on or off.
    solenoid_hpgl = task_share.Queue('f', size = 250, thread_protect = False,
                                      overwrite = False, name = 2)
    
    ## This create the share object is to set the radial set point within each task for any given moment.
    set_point_r = task_share.Share ('f', thread_protect = False, name = "Radial Set Point")
    
    ## This creates the share object is to set the theta set point within each task for any given moment.
    set_point_theta = task_share.Share ('f', thread_protect = False, name = "Theta Set Point")
    
    ## This share object is the error of the radial encoder from its set point to set duty and determine when it has reached the set point. 
    error_r = task_share.Share ('f', thread_protect = False, name = "Radial Position Error")
    
    ## This share object is the error of the theta encoder from its set point to set duty and determine when it has reached the set point. 
    error_theta = task_share.Share ('f', thread_protect = False, name = "Theta Position Error")
    
    ## This create the share object is used to signal when the limit flag on the angular axis is triggered
    limit_flag_A = task_share.Share ('i', thread_protect = False, name = "Flag for Limit Switch A")
    
    ## This create the share object is used to signal when the limit flag on the radial axis is triggered
    limit_flag_B = task_share.Share ('i', thread_protect = False, name = "Flag for Limit Switch B")
    
    ## This creates the share object to signify once both limit flags are true to represent when the system is at the orgin.
    flag_zero = task_share.Share ('i', thread_protect = False, name = "System is zeroed")
    
    ## Creates the motor object for motor of the radial direction
    motor_B = MotorDriver(pyb.Pin.board.PA0, pyb.Pin.board.PA1, pyb.Pin.board.PC1, 5)
    
    ## Creates the motor object for motor of the angualr direction
    motor_A = MotorDriver(pyb.Pin.board.PB5, pyb.Pin.board.PB4, pyb.Pin.board.PA10, 3)
    
    ## Creates the encoder object for encoder of the radial radial direction
    enc_B = EncoderDriver(pyb.Pin.board.PC6, pyb.Pin.board.PC7, 8)
    
    ## Creates the encoder object for encoder of the angualr direction
    enc_A = EncoderDriver(pyb.Pin.board.PB6, pyb.Pin.board.PB7, 4)
    
    ## Create the position control the position of the motor along the angualr axis
    control_theta = PositionControlTask(motor_A, enc_A, error_theta, set_point_theta, .006)    # controller for theta direction
    
    ## Creates the position control the position of the motor along the radial axis
    control_radial = PositionControlTask(motor_B, enc_B, error_r, set_point_r, .025) # controller for radial direction
    
    ## Creaates the limit switch object to interact with the hardware of the switch on the angualr axis
    limit_A = Limit_Switch(pyb.Pin.board.PC2)
    
    ## Creates the limit switch object to interact with the hardware of the switch on the radial axis
    limit_B = Limit_Switch(pyb.Pin.board.PB0)
    
    ## Create the solenoid object to interact with the circuit connected to the solenoid to make it turn on and off
    my_sol = Solenoid(pyb.Pin.board.PC4)
    
    ## THis create the object of the read_plotter file to send it the raw data of the hpgl to be converted to our radial and angualr set points we need.
    my_hpgl = read_plotter.Hpgl(radial_hpgl, theta_hpgl, solenoid_hpgl, 85, 195)
    
    my_hpgl.read_data()
    
    my_hpgl.convert_data()
    
    ## This is the numerical value of our orgin of our system as it offset from the center of rotation, this value is measured in millimeters.
    origin = my_hpgl.convert_point(210,297)
    
    ## This creates a flag that is a share object of when the set point is reached along the angualr axis.
    flag_theta = task_share.Share ('i', thread_protect = False, name = "Flag Theta Set is reached")
    
    ## This creats a flag that is a share object of when the set point is reached along the radial axis.
    flag_radial = task_share.Share ('i', thread_protect = False, name = "Flag Radial Set is reached")
    
    print(origin)
    
    ## Task 1 used to operate motor 1 function task
    task1 = cotask.Task (update_pwm_radial, name = 'Radial Position Control', priority = 1, 
                             period = 10, profile = True, trace = False)
     
    ## Task 2 used to operate motor 2 function task
    task2 = cotask.Task (update_pwm_theta, name = 'Theta Position Control', priority = 1, 
                             period = 10, profile = True, trace = False)
      
    ## Task 2 used to operate motor 2 function task
    task3 = cotask.Task (get_setpoint_r, name = 'Radial Set Point Control', priority = 1, 
                             period = 10, profile = True, trace = False)
    
    ## Task 2 used to operate motor 2 function task
    task4 = cotask.Task (get_setpoint_theta, name = 'Theta Set Point Control', priority = 1, 
                             period = 10, profile = True, trace = False)
    
    ## Task 2 used to operate motor 2 function task
    task5 = cotask.Task (zero_position, name = 'Zero Position', priority = 1, 
                             period = 10, profile = True, trace = False)
    
    gc.collect()
        
    # Add tasks to cotask schedular list
    cotask.task_list.append (task1)
    cotask.task_list.append (task2)
    cotask.task_list.append (task3)
    cotask.task_list.append (task4)
    cotask.task_list.append (task5)
    
    while True:
        cotask.task_list.pri_sched()

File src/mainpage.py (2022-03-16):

"""!
   @file                       mainpage.py

   @mainpage                   Main Page

   @section sec_intro1         Software Design
                               Our program will consist of the task functions zero_position(), update_pwm_radial(), update_pwm_theta(), get_setpoint_r(), and get_setpoint_theta(). The zero_position() task sets the duty cycle of the motor controlling the radial direction to 45 so the pen moves towards home base (our y-offset) until it hits the limit switch. Once the limit switch triggers, the zero_position() task enters an empty state and triggers the position control phases to begin. The update_pwm tasks facilitate position control by setting the duty cycle of each respective motor based on the error between our encoder position and setpoint adjusted by our proportional gain value. As each encoder gets closer to its desired position, the duty cycles will be decreasing to reach a final position without overshooting via closed loop position control. The update_pwm tasks also check if a desired setpoint has been reached by an individual motor. In this case, that motor’s duty cycle is set to zero until the other motor reaches its setpoint. Once all setpoints have been reached, the duty cycle of each motor is set to zero to terminate the program. The get_setpoint() tasks are responsible for iterating to the next desired HPGL setpoint for each motor once the previous setpoint has been set. These tasks also flag once a setpoint has been reached, signaling to the updat_pwm tasks to stop the respective motor until the other motor's setpoint flag is triggered. 
                               All in all, our system works by performing closed loop position control on each motor individually, each having its own gain value and setpoints. The setpoints are acquired from HPGL and converted from raw dpi into encoder ticks that we specify for each motor. The setpoints for our radial and theta coordinates are iterated through once each motor has reached its desired setpoint within reasonable error. All tasks are facilitated by a main file, storing data in shares and queues so tasks and other files can share data. While each motor is being controlled, we integrated a solenoid to control the orientation of the pen acquired from HPGL setpoint data. Additionally, we use a limit_switch to ensure our pen position is set at the right zero point and does not move too far in the radial direction to damage our system. The main file runs all tasks through the task scheduler from the file co_task().
                               
   @section subsec_intro2      Task Diagram and Finite State Machines
                               Below is the Task Diagram of all tasks used to control the pencil position.
                               
                               \image html TaskDiagram_FinalProj.jpg
                               
                               Below is the Finite State Machine for our the position control file of one motor.
                               
                               \image html Fsm_TermProj.jpg
                        
   @section subsec_intro3      Example System Response and PuTTY command window
                               A link to an exapmle system response can be found here: https://youtu.be/lQJ4eko8kKs
                               A link to an example PuTTY command window can be found here: https://youtu.be/Qp4Me-iPOtM
                               In our PUTTY output we begin by zeroing the pen position, showing the duty cycle set to 45%. Once the position has been zero'd we begin to see print statements of our current set position for each motor. You can see the current position chasing the current set point, and once the setpoint is reached you can see the program increments to next set point. These print statements helped us in debugging, showing that our set point does in fact change once the error criteria is reached. 
    @author                    Jameson Spitz
   @author                     Jacob Wong
   @author                     Wyatt Conner

   @copyright                  CC BY

   @date                       March 10, 2022
"""

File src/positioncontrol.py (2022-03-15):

"""!
@file positioncontrol.py
Control Motor's position based on desired HPGL set points. The file can check if the error between a motor position
and the setpoint is within reasonable limits and flag for the next setpoint. We use a simple proportional controller to
set a proper duty cycle based on the magnitude of the error.
@author Jacob Wong
@author Wyatt Conner
@author Jameson Spitz
@date   3-Mar-22
@copyright by Jameson Spitz all rights reserved
"""
# from motordriver import MotorDriver
# from encoderdriver import EncoderDriver

class PositionControlTask():
    """!
    This class contains the methods to create a feed back control system using a 
    motor and encoder. the motor is acting as the the plant of the system and the 
    encoder is the sensor of the system. This class
    has the methods to actually complete this by checking the position and updating the
    error of the system and calculating the new data of the sy
    """
    
    def __init__(self, Motor, Encoder, error, set_point, gain):
        """!
        This method initializes the position control object so we can create multiple
        objects for various encoder motor systems. This also initalizes our object variables
        """
        ## This variable passes the motor object into the position control object
        self.Motor = Motor
        ## This variable passes the encoder object into the position control object
        self.Encoder = Encoder
        ## This initilizing our controllers gain as zero as it will be referenced for other methods
        self.gain = gain
        ## This initilizes the desired position we want the motor to achieve
        self.setpoint = set_point
        ## This initilizes the error variable to represent the difference of position to our actual position
        self.error = error
    
    def set_point(self):
        """!
        This method is used to set the desired position of the encoder for the motor
        to achieve, this is the input to our control system. It is set up to take this value
        in units of encoder ticks. Each rotation is 16,000 ticks. 
        """
        try:
            self.setpoint = float(input('Enter desired position value in ticks \n'))
            while self.setpoint == 0:
                self.setpoint = float(input('The set point cannot be zero enter a valid value \n'))
        except:
            print('Please enter a valid number for the set point')
            
    def set_gain(self):
        """!
        This method is used to set the gain of the porportional controller for the
        position controller. This gain is multiplied by the error of the posisiton
        to calculate the duty cycle to send to the motor. 
        """
        try:
            self.gain = float(input('Enter desired porportional gain value \n'))
        except:
            print('Please enter a valid number for the gain')
    
    def position_control(self):
        """!
        This method used in an external loop from the task scheduler to control the motor and encoder
        pair for the desired location. This method updates the encoder position,
        and calculates the error of system with the difference of the current
        position to the desired position, this is multiplied by the gain to calculate
        the duty cycle of the motor each iteration. 
        """
        # Update the encoder position
        self.Encoder.update_delta()
        
        ## This variable is used to store the ticks value of the encoder
        self.position = self.Encoder.get_position()
        
        if(self.setpoint.get() == 0): ## Edit with zeroing function
            self.error.put(0)
        else:
            self.error.put((self.setpoint.get() - self.position))
        
        if self.error.get() > 0:
            ## Duty is represents the duty cycle being sent to the motor object
            self.duty = -1*self.gain*self.error.get() - 25
        elif self.error.get() < 0:
            self.duty = -1*self.gain*self.error.get() + 25
        else:
            self.duty = 0
        
        self.Motor.set_duty_cycle(self.duty)
        
        print('Position ----------------: ', self.position)
        print('Setpoint ----------------: ', self.setpoint.get())
        
    def check_error(self):
        """!
        This method checks that our error in units of ticks is within reasonable limit. If the error is 
        within that reasonable limit, the method returns a flag for the main file to iterate to the next setpoint.
        """
        if(abs(self.error.get()) < 3000):
           # print('!!!!!!!!!!!!!!!!Checkpoint!!!!!!!!!!!!!!!!!!')
            return True
        else:
            return False
    
    

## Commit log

2022-02-25 CAD update
    [Assembly_V2.SLDASM, Base_Plate.SLDPRT, Clevis Joint.SLDPRT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]
2022-03-06 supporting drivers and main
2022-03-07 working motors!
